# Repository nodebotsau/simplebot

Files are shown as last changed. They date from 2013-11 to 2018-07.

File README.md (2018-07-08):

# SimpleBot



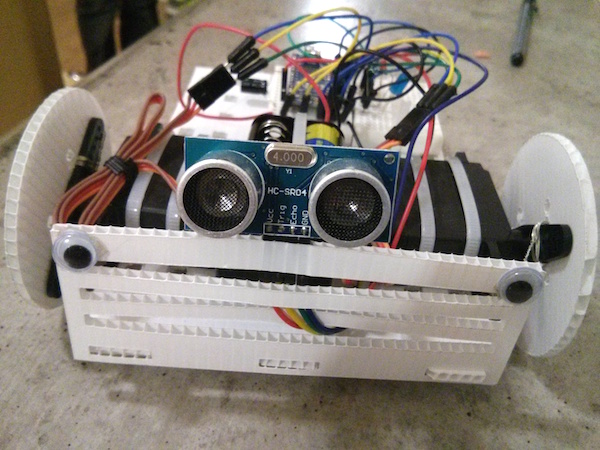
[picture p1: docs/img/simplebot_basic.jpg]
SimpleBot


## Overview

This is one of the most simple robots you can make. Features are:

* quick to put together (about an hour)
* very hackable (it can be built with cardboard, corflute or laser cut acrylic
or wood so very easily modifiable)
* can move pretty fast (at full tilt it will go about half a metre a second -
faster if you have more juice for the motors!)
* very extendable (much of the magic happens in code and sensors can be easily added)
* Cheap (costs less than AUD$100 which is very cheap for your first robot)

This bot is an adaptation of the excellent [SumoBot Jr](https://github.com/makenai/sumobot-jr/)
made by [Paweł Szymczykowski](http://twitter.com/makenai) but doesn't require
laser cutting wood or plastic to make. However you can laser cut it if you want
something a bit more long lasting.

## Capabilities

The SimpleBot can be tethered over USB or controlled via Bluetooth Serial or
over the network using WiFi. Your computer will do all the hard work of
control processing and interface control etc and just send messages to the
board to steer it.

If you get really sophisticated you can make it have some AI.

This is the very first prototype, put together in about 30 minutes one evening.

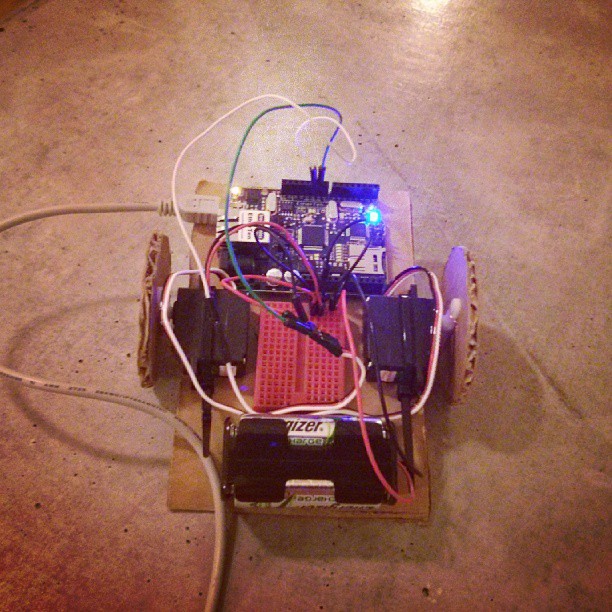
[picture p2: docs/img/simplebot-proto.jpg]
SimpleBot


As this is such a simple robot, once you've got it working you can then extend
it to make it much more capable including becoming wireless. This one has been
extended with a wifi module to untether it from your computer..

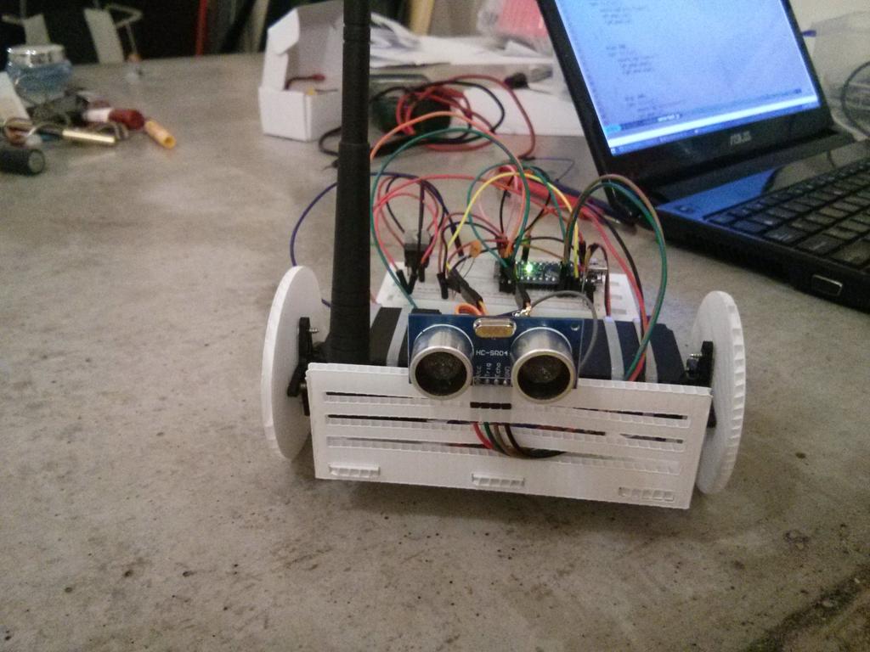
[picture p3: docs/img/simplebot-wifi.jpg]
SimpleBot MkII


Once you understand how things work you can reuse all of the components to
make a bigger, badder, faster robot and switch the cardboard for more durable
elements such as laser cut wood or plastic if you desire.
We've even [supplied the SVG and DXF files to do exactly that](/physical).

Add a raspberry pi and you get a SimplePiBot which can be made fully autonomous.

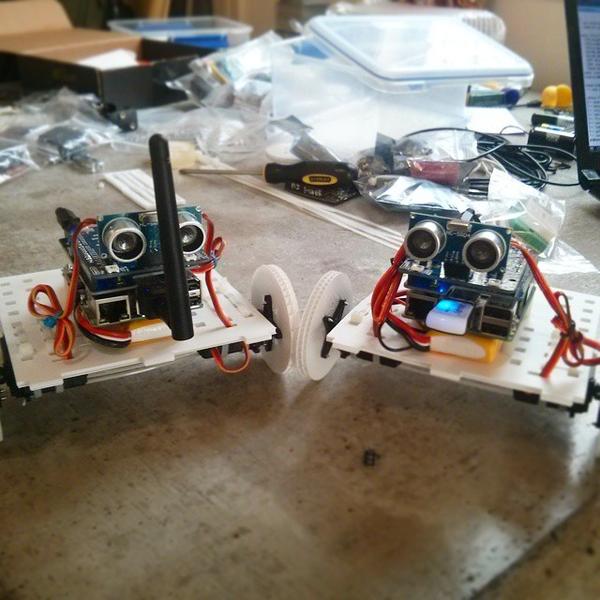
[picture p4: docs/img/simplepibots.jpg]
SimplePiBot


## Materials needed

The following are the various components you need to get hold of to make a basic
SimpleBot. If you're making this at a NodeBots event you'll have a set of
components in your kits.

|  # | Component | Notes |
|:--:|---|---|
|  1 | Arduino | We use Nanos because they are small and inexpensive (and light) but any arduino will do |
| 10 | M-M Jumper wires | The more the better but 10 will be enough to build with |
|  2 | DC Motors | These are common - get ones with wheels & gears |
|  1 | Battery pack | LiPo or 4xAA - about 5V is what you're after |
|  1 | Mini breadboard  | Smaller is better |
| 10 | Cable ties | 3-4mm wide and about 100-200mm long is a good size to work with. The more the better |

Other things you might want to add to your bot:

* Laser pointer to make an annoying cat toy.
* Stickers to bling out your bot.
* Spikes to take out others; Ben Hur or Mad Max style.
* USB WebCam if you want to give your bot some vision.
* USB cable extender if you want some range.
* Bluetooth or wireless modules to remove the USB cable.
* An Ultrasonic sensor to do obstacle detection
* Reflectance sensors to do line following

# Installation and setup

Start with the [installation process outlined here](https://github.com/nodebotsau/nbdau/blob/master/setup.md)
if you haven't already done so.

## Install the code dependencies

Clone the repo and install everything from here:

```
git clone https://github.com/nodebotsau/simplebot.git
cd simplebot
npm install
```

## Flashing the arduino

Use `interchange` to install the firmware to the arduino. Plug the arduino in
and then run the following command from your terminal.

```
interchange install hc-sr04 -a nano --firmata
```

Assuming you get no errors, you're good to go on that front.

## Run a basic blink program

Next, to test you've got Firmata running, run a basic blink program with the following command: 

```
node examples/blink.js
```

If it all goes well. You'll see a blinking LED positioned next to the L on your arduino.

```
[ ] RX
[ ] TX
[*] POW 
[*] L     <--- this light will start flashing
```

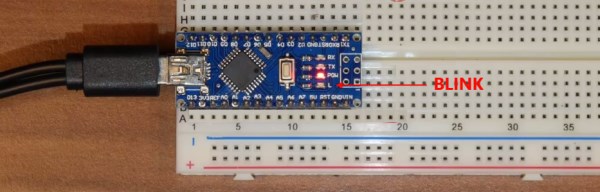
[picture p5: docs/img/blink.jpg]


Open the [`examples/blink.js`](examples/blink.js) program in an editor and look at the code. Its currently set to blink every 500ms. 

Try changing this to 100ms and see if it blinks faster now.

```js
board.on("ready", function() {
  var led = new five.Led(13);
  led.blink(500);  //  <--- try changing this value see if it blinks faster/slower
});
```

## Build a SimpleBot

You can go in a few different directions with the SimpleBot. Details for the
different styles can be found below however the common principles are
discussed in the next section.

* [SumoBot](docs/sumobot.md)
* [Line Follower](docs/linefollower.md)
* [Obstacle avoider](docs/obstacleavoider.md)

### Differential drive

Each SimpleBot is a little different because it's yours but the general principles
are the same. You have two motors, each of which drive a wheel - this is called
[differential drive](https://en.wikipedia.org/wiki/Differential_wheeled_robot) -
and the combination of these working together will drive the robot forward, backwards
and turn on the spot each way.

Use cable-ties (zip ties) to join everything to the chassis.

If you want to see a video explaining this in more detail there's a version
on [you tube](https://www.youtube.com/watch?v=KoACCjtkHIg) (this uses servos on
an older Mark III SimpleBot but the principle holds).

### Basic wiring

The wiring diagrams are provided here:

Schematic:

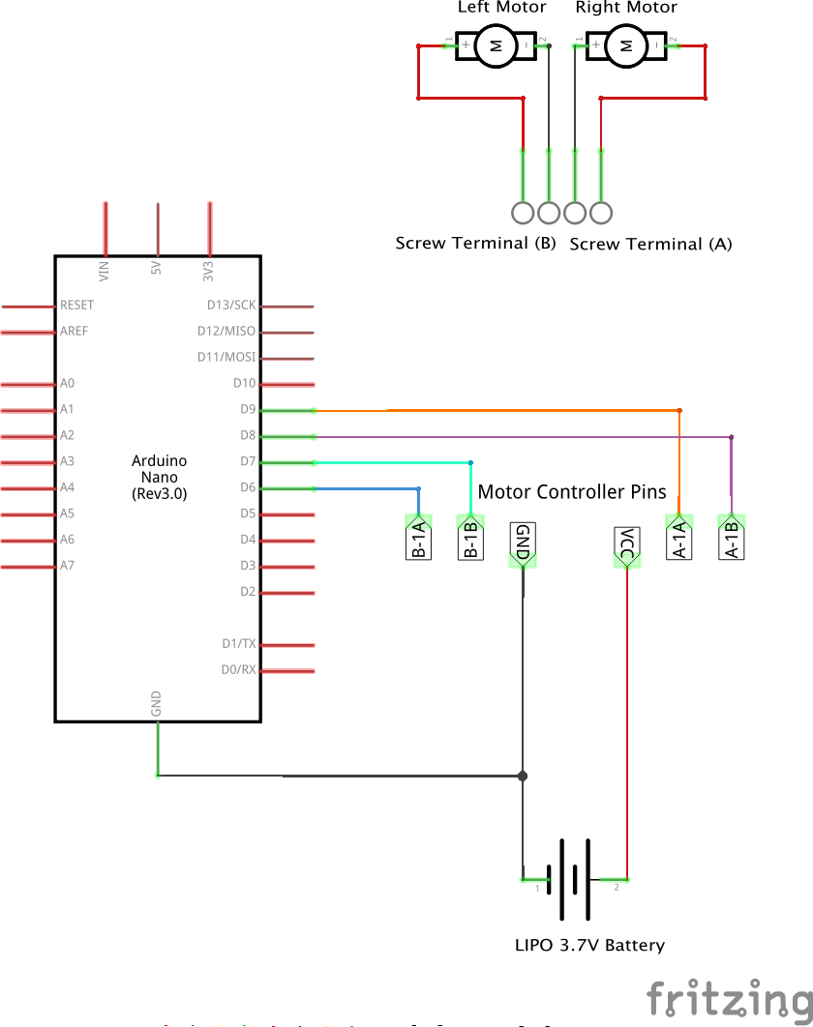
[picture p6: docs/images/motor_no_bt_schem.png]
SimpleBot schematic


# Examples

## A simple drive example

In the `examples` folder you can see an example called `motors.js` or
`servos.js` - choose the version depending on your motor types. This is
a very simple control example which uses the arrow and space keys on the keyboard
to drive the SimpleBot around.

Simply run:

```shell
node examples/motors.js SERIAL_DEVICE
```

```shell
node examples/servos.js SERIAL_DEVICE
```

Where `SERIAL_DEVICE` is the path to the serial port (eg `/dev/tty/USB0`).

You should now be able to drive your robot around happily. Go get a few friends
to build one too and you can have SumoBot Battles.

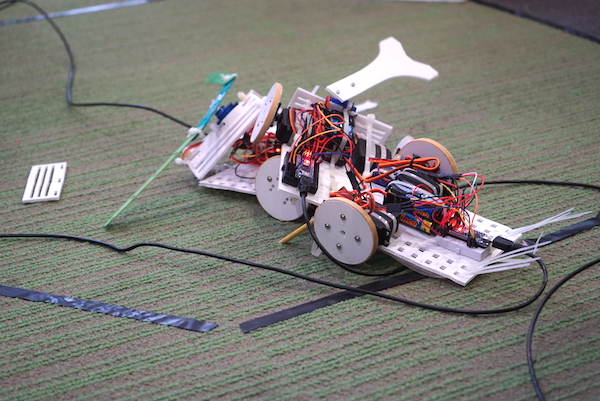
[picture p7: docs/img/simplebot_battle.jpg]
A simplebot battle royale at NodeBots Day


### Tuning servos

If you are using servos and they don't entirely stop then tune the stop value in the code by
setting a LSTOP and RSTOP value that is a little either side of 90 (this is
because CR servos are a hack and may need some tuning).

## Driving over Bluetooth

You can use bluetooth to drive the simplebot.

Get a bluetooth module and configure it. This is a mandatory step before you can
do it properly..

Per [this wiki entry in J5](https://github.com/rwaldron/johnny-five/wiki/Getting-Started-with-Johnny-Five-and-JY-MCU-Bluetooth-Serial-Port-Module)

### Wiring for BT.

Connect the BT Module TX pin to the Arduino RX pin and the BT Module RX pin to
the Arduino TX pin and you should be ready to go. Note that if you need to
flash the arduino or anything you need to unplug the BT module.

### Connecting

Once you've got your bluetooth set up, pair it with your computer so it appears
as a serial device.

Simply go:

```
node examples/motors.js /dev/tty.SERIALPORT
```

Changing the device path to whatever yours is to the Bluetooth Module. You
should now be able to drive using wireless over bluetooth just the same as
using a USB cable.

## Game controller

If you happen to have a playstation controller then you can use the
sb-controller.js example to drive your simplebot using a console controller
which is pretty cool.

# LICENSE NOTES

This SimpleBot repo is licensed using the MIT license for all components.

Firmata implementations are modifications of
[https://github.com/firmata/arduino/](Firmata for Arduino) by
[https://github.com/soundanalogous](Jeff Hoefs @soundanalagous) and others and
is used according to the GPL.

Firmata modifications include merged components of
the [https://github.com/jgautier/arduino-1/tree/pulseIn](pulseIn code) as
created by [https://github.com/jgautier](Julian Gautier @jgautier).

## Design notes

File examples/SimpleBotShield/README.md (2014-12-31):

# Using the SimpleBot Shield

If you have a SimpleBot shield you will need an arduino to go with it.

Key features of the shield are:

* Servo headers broken out for Left and Right wheels on pins 9 & 10
* Additional headers broken out for pins 2,3,5,6 using servo pin out style (sig, 5v, gnd)
* 4xWS2812b RGB LEDs (NeoPixels) on the corners of the board attached to pin 6
* Ultrasonic sensor broken out attached to pin 8
* Breakouts for Analog pins 1-5 using screw terminals
* I2C breakout for optional IMU9 module 

## Populating the board

Here are the [build instructions for the board](http://www.openhardwareconf.org/wiki/SimpleBot_Shield_Assembly).

More [detailed instructions](http://www.openhardwareconf.org/wiki/Surface_Mount_Assembly_for_SimpleBot_Shield) on soldering the WS2812 LEDs is available here.

## Preparing custom firmata

To use this shield in total you will need a custom version of firmata that
comprises all the additional libraries you need to make it work. This ships
as part of this repo in the firmware directory. You will need to use ino tool to
compile and upload this to the board so [follow the getting started directions](http://inotool.org/#installation) for
ino tool before attempting the next component.

To install firmata (and install all node dependencies also) follow the directions below.

```
cd ~
git clone https://github.com/nodebotsau/simplebot
cd simplebot
npm install
cd firmware/ino/SBSFirmata
ino clean && ino build -m uno
```

You should see the output of the build sequence and get a positive response from ino 
as below:

```
Searching for Board description file (boards.txt) ... /home/pi/arduino-1.0.5/hardware/arduino/boards.txt
Searching for Arduino lib version file (version.txt) ... /home/pi/arduino-1.0.5/lib/version.txt
Detecting Arduino software version ...  1.0.5 (1.0.5)
Searching for Arduino core library ... /home/pi/arduino-1.0.5/hardware/arduino/cores/arduino
Searching for Arduino variants directory ... /home/pi/arduino-1.0.5/hardware/arduino/variants
Searching for Arduino standard libraries ... /home/pi/arduino-1.0.5/libraries
Searching for make ... /usr/bin/make
Searching for avr-gcc ... /usr/bin/avr-gcc
Searching for avr-g++ ... /usr/bin/avr-g++
Searching for avr-ar ... /usr/bin/avr-ar
Searching for avr-objcopy ... /usr/bin/avr-objcopy
src/SBSFirmata.ino
Searching for Arduino lib version file (version.txt) ... /home/pi/arduino-1.0.5/lib/version.txt
Detecting Arduino software version ...  1.0.5 (1.0.5)
Scanning dependencies of src
Scanning dependencies of Servo
Scanning dependencies of neopixel
Scanning dependencies of ws2812
Scanning dependencies of Wire
Scanning dependencies of arduino
src/Firmata.cpp
src/SBSFirmata.cpp
Servo/Servo.cpp
Linking libServo.a
ws2812/ws2812.cpp
Linking libws2812.a
Wire/utility/twi.c
Wire/Wire.cpp
Linking libWire.a
neopixel/Adafruit_NeoPixel.cpp
Linking libneopixel.a
arduino/wiring_pulse.c
arduino/wiring_analog.c
arduino/WInterrupts.c
arduino/wiring_shift.c
arduino/avr-libc/malloc.c
arduino/avr-libc/realloc.c
arduino/wiring_digital.c
arduino/wiring.c
arduino/WString.cpp
arduino/new.cpp
arduino/Print.cpp
arduino/main.cpp
arduino/Stream.cpp
arduino/CDC.cpp
arduino/HID.cpp
arduino/USBCore.cpp
arduino/WMath.cpp
arduino/Tone.cpp
arduino/HardwareSerial.cpp
arduino/IPAddress.cpp
Linking libarduino.a
Linking firmware.elf
Converting to firmware.hex
```

Assuming no errors go ahead and upload using one of the options below.

If just a standard Arduino then:

    ino upload -m uno

If you're using a PiLeven then:

    ino upload -m uno -p /dev/ttyS99

You will get something similar to the following output:

```
Searching for stty ... /bin/stty
Searching for avrdude ... /home/pi/arduino-1.0.5/hardware/tools/avrdude
Searching for avrdude.conf ... /home/pi/arduino-1.0.5/hardware/tools/avrdude.conf
Guessing serial port ... /dev/ttyACM0

avrdude: AVR device initialized and ready to accept instructions

Reading | ################################################## | 100% 0.00s

avrdude: Device signature = 0x1e950f
avrdude: reading input file ".build/uno-620a679d/firmware.hex"
avrdude: writing flash (17628 bytes):

Writing | ################################################## | 100% 3.16s

avrdude: 17628 bytes of flash written
avrdude: verifying flash memory against .build/uno-620a679d/firmware.hex:
avrdude: load data flash data from input file .build/uno-620a679d/firmware.hex:
avrdude: input file .build/uno-620a679d/firmware.hex contains 17628 bytes
avrdude: reading on-chip flash data:

Reading | ################################################## | 100% 2.47s

avrdude: verifying ...
avrdude: 17628 bytes of flash verified

avrdude: safemode: Fuses OK

avrdude done.  Thank you.
```

If there's no errors then you now have the relevant firmata on your arduino for the
SimpleBot Shield.

## Using the examples

AS part of the repos, three examples are provided that are designed to work 
specifically to the shield. These are located in the same folder as this
README and are described below

All examples should be called from the root of the repo after having executed:

```
npm install
```

In order to install the node dependencies.

### simplebot.js 

This is a simple driving example taking input from the keyboard to drive your
SimpleBot around. The arrow keys drive it forward, backwards and turn it
left and right. Space will stop it.

To run, use the command below, substituting /dev/ttyS99 for the port of your
arduino for your environment.

```
nodejs examples/SimpleBotShield/simplebot.js /dev/ttyS99
```

### ping.js

This example shows how the ping sensor works and reports back the range in
cm and inches to an obstacle. 

To run, use the command below, substituting /dev/ttyACM0 for the port of your
arduino for your environment.

```
nodejs examples/SimpleBotShield/ping.js /dev/ttyACM0
```

Output will look like this (use Ctrl+C to quit):

```
1420024159594 Connected /dev/ttyACM0 
1420024159599 Repl Initialized 
>> Object is 15.259 cm away
Object is 5.98 inches away
Object is 33.431 cm away
Object is 13.1 inches away
```

### np.js

This example shows how the neopixels can be lit and will move a single pixel
clockwise around the board moving through different colours.

To run, use the command below, substituting /dev/ttyACM0 for the port of your
arduino in your environment.

```
nodejs examples/SimpleBotShield/np.js /dev/ttyACM0
```

If you review the code you can see a single pixel is being updated and cycling
through various color names. Pixel can take a few options as illustrated below:

```
// strip.color() applies to the whole set of LEDs
// strip.show() is required once you have made your color manipulations in order
// to latch the LED strip and make them work.

strip.color("#ff0000"); // set whole strip red

// You can use HTML CSS color names and RGB values will be created
strip.color("teal"); // sets strip to a blue-green color.

// You can also use RGB values if you desire as shown below
strip.color("rgb(0, 255, 0)"); // sets strip to green.

// individual pixels can be addressed as well.
var p = strip.pixel(1); // get second LED

// and colors work just the same way on individual pixels too.
p.color("#0000FF"); // set second pixel blue.

// calling color() by itself will return an object with the current color
p.color(); // returns {r:0, g:0, b:255, hexcode:"#0000ff", color:"blue"}
```

## Going further

There are plenty of things you can do with a simplebot shield for example:

* Use the pixels to give you blinkers when you turn
* Back up when you get too close to an obstacle.
* direct the LEDs and use it to signal another SimpleBot
* Make a bot that dances and lights up when you get a tweet.

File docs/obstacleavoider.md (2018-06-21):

# Physical layout and design considerations for an obstacle avoiding robot

This document explains some of the design considerations you might want to
think about when building your robot.

## Electronics

The core electronics are as discussed for the basic SimpleBot build. You should
have a robot you can control with a keyboard to drive around.

### Additional components

* 1x Ultrasonic range finder

The diagram below shows the electronics schematic for a basic set up.

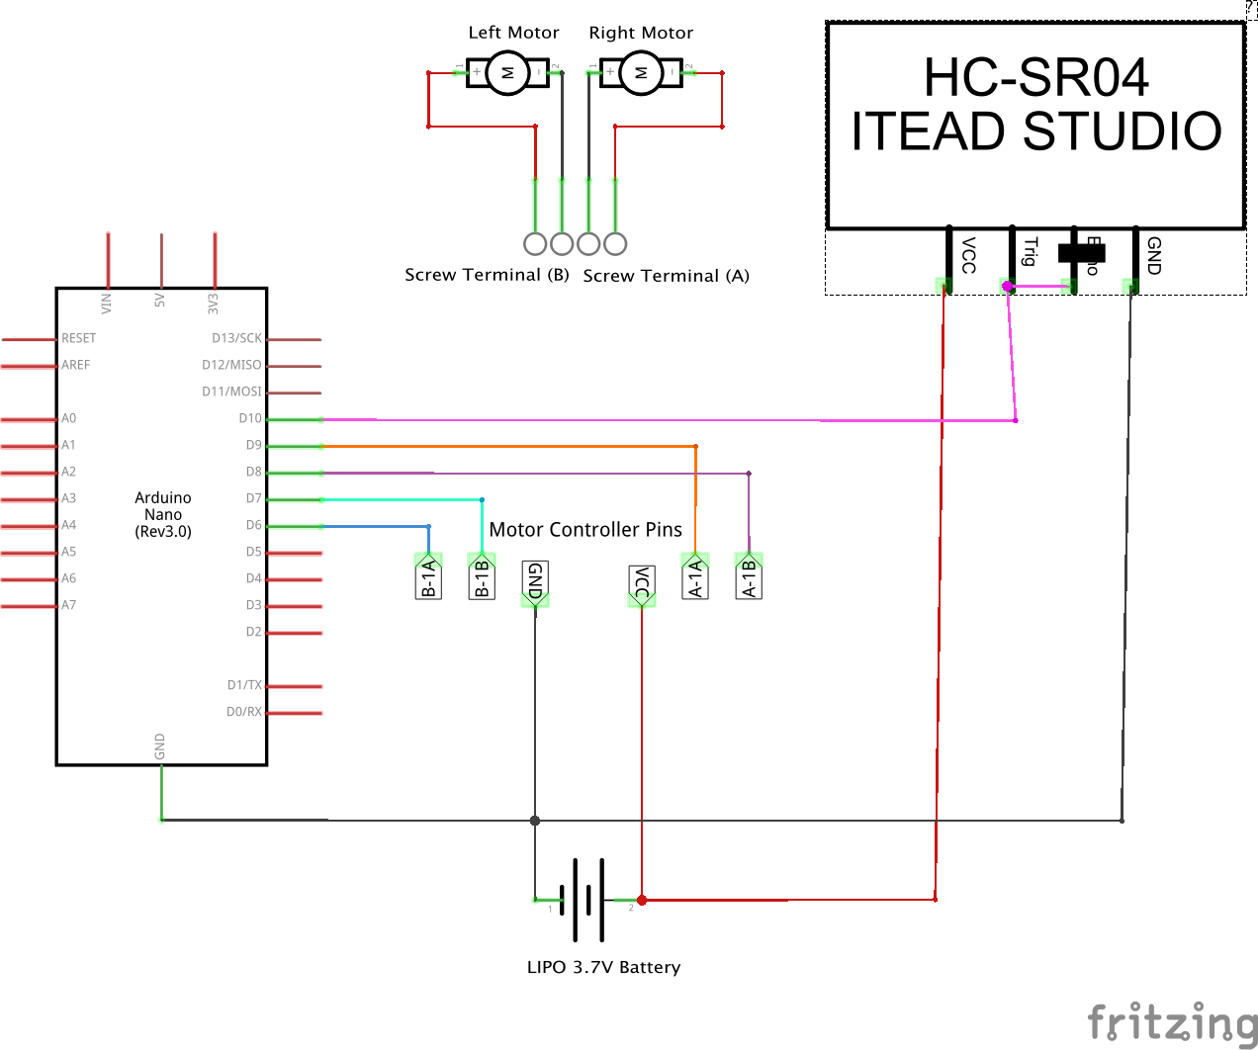
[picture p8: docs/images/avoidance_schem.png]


Note that the echo and trigger pins on the sensor are wired to the same pin
as the arduino can use both.

## Physical modifications

As you see the range finder looks like a pair of eyes and it does "see" like
a bat. As such you want to mount these on the front of your robot so they are
unobstructed. Cable ties work very well for this.

## Examples

In the `examples/simplebot-avoidance.js` file you can see a basic example that
will allow you to drive around until you get within 10cm of an obstacle and
then the SimpleBot will stop.

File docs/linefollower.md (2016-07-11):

# Physical layout and design considerations for a Line Following robot

This document explains some of the design considerations you might want to
think about when building your robot.

## Electronics

The core electronics are as discussed for the basic SimpleBot build. You should
have a robot you can control with a keyboard to drive around.

### Additional components

* 2x Reflectance sensors

The diagram below shows the electronics schematic for a basic set up.

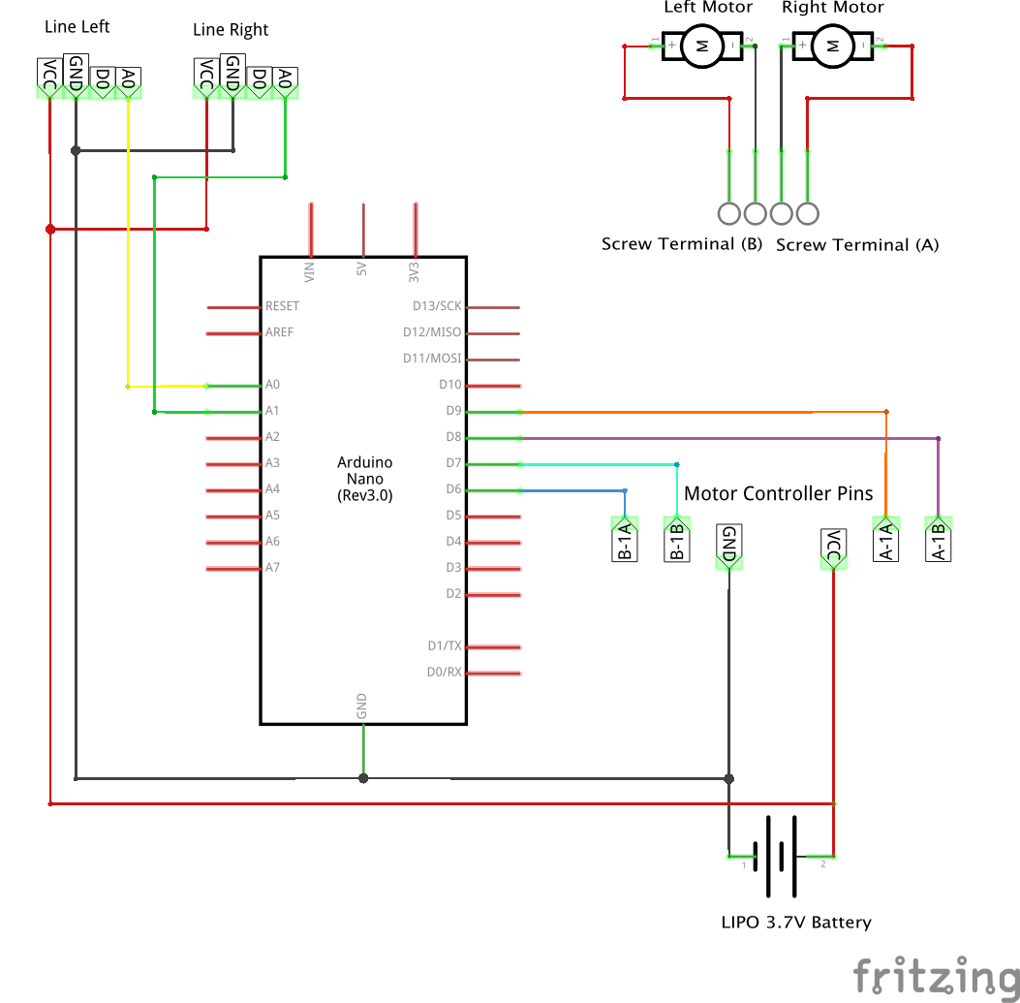
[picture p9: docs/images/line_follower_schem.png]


## Physical modifications

The reflectance sensors need to be pretty close to the ground, less than 1cm
is ideal. Mount them the same distance apart as the tape you'll be detecting.
What you want is for both sensors to be on the tape at the same time and you
can then tell when you are drifting off.

## Calibrating your sensors

Once you have the sensors wired up run `examples/calibrate-line.js` and
then slowly turn your bot back and forth over the line in order to get a sense
of what the minimum and maximum numbers it's seeing.

If you have a really contrasty surface you should get numbers close to 1023 for
full reflection and close to 0 for full absorption. The reality is you'll see
something inside that range.

Note down numbers that give you fairly definitive "on the line" and "off the line"
values.

## How line following works

The most simple line following algorithm is this:

```
// precondition: Both sensors start on the line

loop:
    drive both motors forward
    if (left sensor is off line):
        turn off right motor
    if (right sensor is off line):
        turn off left motor
```

This very simple code will check each of the sensors every time it loops. If
the sensor is on the line then that wheel will stay on as you want it to drive
forwards. If it comes off the line however, you turn the *opposite* wheel off
so that the wheel on the same side of the robot as the sensor is keeps driving.
This will pivot the bot back towards the line and it should move forwards again.

This algorithm is a naive approach and it does work but it is prone to
overshooting and not handling sharp turns. You can make it better with more
line sensors but also by reading the drift to see how much you've drifted or
for how long, this allows you to determine how much to turn back.

## Examples

In the `examples/simplebot-line.js` file you can see a basic example of this
algorithm in practice. If you put your bot on the test track and and run this
code you should see it slowly drive around the track, correcting its position
if it starts to drive off.

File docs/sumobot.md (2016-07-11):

# Physical layout and design considerations for a SumoBot

This document explains some of the design considerations you might want to
think about when building your robot.

## Electronics

The diagram below shows the electronics schematic for a basic set up.

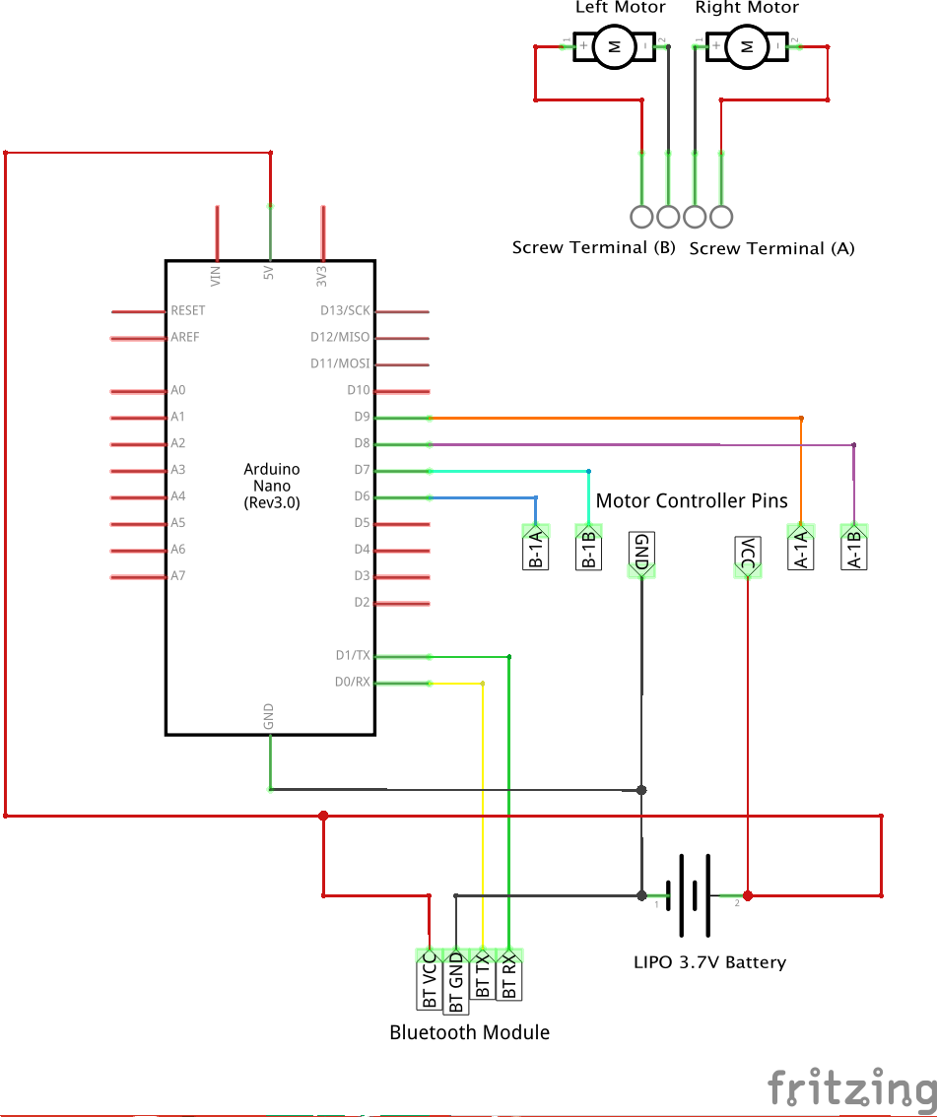
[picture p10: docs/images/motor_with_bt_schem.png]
Full schematic


If you do this however, once you move to bluetooth you may run into power
issues where the arduino resets on you. This will be particularly noticeable
when the battery is running flat. So what can you do?

First, keep your battery charged up. You have a charger to do exactly that so
use it. A full LiPo battery gives a nice solid voltage everything can use so
charge between tests and battles.

The second option is to use two batteries. One for your controllers and one for
your motors. The schematic for this is mostly the same except the VCC and GND
lines for your motors and servo connect to the second battery instead.

## Design styles

The maximum size of your bot is 25cm x 25cm x25cm - it has to fit inside that
to go in the ring. Too big and you're disqualified.

There are several design archetypes:

### The Wedge

This is a triangular wedge shape with the main aim being to stay low, move
fast and get under your opponent and run them out of the ring.

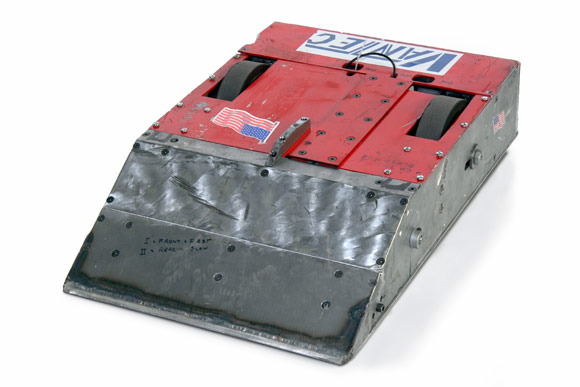
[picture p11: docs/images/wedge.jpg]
A perfect example of the Wedge


To do this effectively:

* Go as light as possible - everything extraneous must be removed
* Attempt to deliver as much speed as possible. This will affect your steering so
drivers need to practice rapid changes of direction and control.
* Traction is critical - when hit an opponent you need traction, make sure
your wheels will grip the floor.
* You need a wedge - it sounds obvious but your whole robot needs to be a wedge
to effectively slide under your opponent. Fabrication of this is critical.

Tactics:

The wedge is all about speed and out manoeuvring your oppenent, especially
those who are slow or have poor turning capability. Look for areas on the
opponent that are raised that will allow you to get underneath. Attack from a
weak side and go fast - don't be afraid to peel off and come back for another run.

### The Sumo

This design calls for weight. You'll move more slowly but with more mass. The
aim is to use your superior weight advantage to push the other opponent out
of the ring.

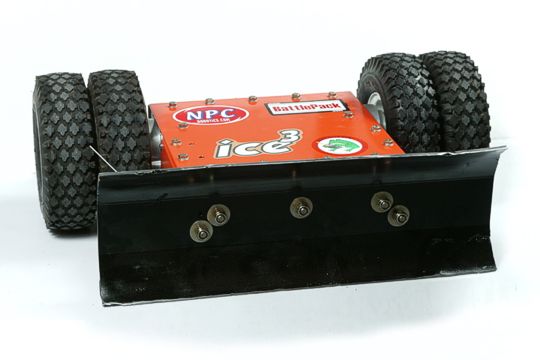
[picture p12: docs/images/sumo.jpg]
A tractor style design. Push, push, push!


To do this effectively:

* Look how you can weight your whole robot. Avoid just weighting one part as
this will make you unbalanced.
* You need traction. You're going to go slow, so deliver all the force you can
to your wheels.
* Protect your flanks - your turning speed will be poor so look at ways to
protect your sides (or better yet, make your bot usable in any direction not just
forwards).
* Snarl your opponent - if your opponent can't move then you can just grind them
out of the ring.

Tactics:

Slow and steady wins the bout. Stay to the middle until your opponent is nearby
then wait for them to try and attack you. Make sure you meet them head on and
then use your superior weight to just push them out of the circle. Don't get
caught on the edge.

### The flipper

Hard to pull off effectively, this design is all about winning in style. The aim is to
make a section of your bot that can use servos to flip an opponent. Once they
are incapable of moving, it's a simple task to push them out.

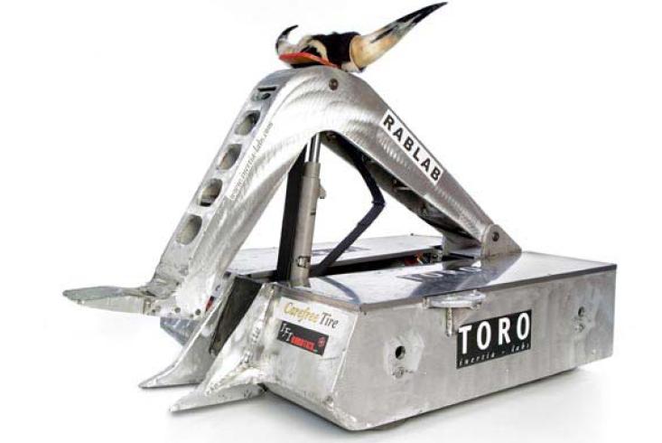
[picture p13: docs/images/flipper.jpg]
You definitely don't want to be anywhere near the front of this


To do this effectively:

* Keep your servo movement small. Servos move at a fixed speed and you want
this to happen fast to catch your opponent off guard. Use mechanical means to
amplify your servo movement into bigger actions.
* Practice your flips against things. It sounds obvious but does your flipper
flip?

Tactics:

Your objective is to close front on and then get your flipper under your
opponent. From there, ACTIVATE and turn that other bot over. Once you've
incapacitated your opponent, just push them out. Your flipper is your key
weapon so make sure you're bringing it to bear on your opponent.

### The whirlygig

This is possibly the craziest design, but pulled off well and it's brutally
effective. You aim is the wholesale destruction of your opponents' electronics
by using a whirling arm mounted on your bot.

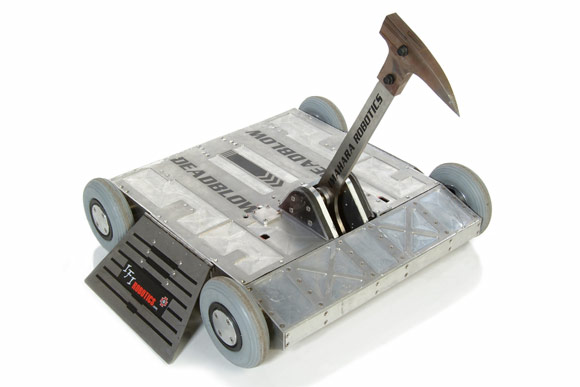
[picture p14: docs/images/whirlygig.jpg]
The pickaxe is a classic of this style


To do this effectively:

* Use servos attached to choppers or other mechanical means of wrecking your
opponent's systems.
* It makes you unbalanced but the higher you can come over the top of your
opponent the more chance you have to rip something important out of their
robot.
* Some particularly devastating whirlygigs just spear their opponent then drop
them outside the ring.

Tactics:

You really only have one objective, close with your opponent and unleash your
chopper, smasher, grabber or whirler as fast and as frequently as possible in
an attempt to maximise damage. A few stray wires ripped out and your opponent
will be dead in the ring. Use that opportunity to just ram them out of it.

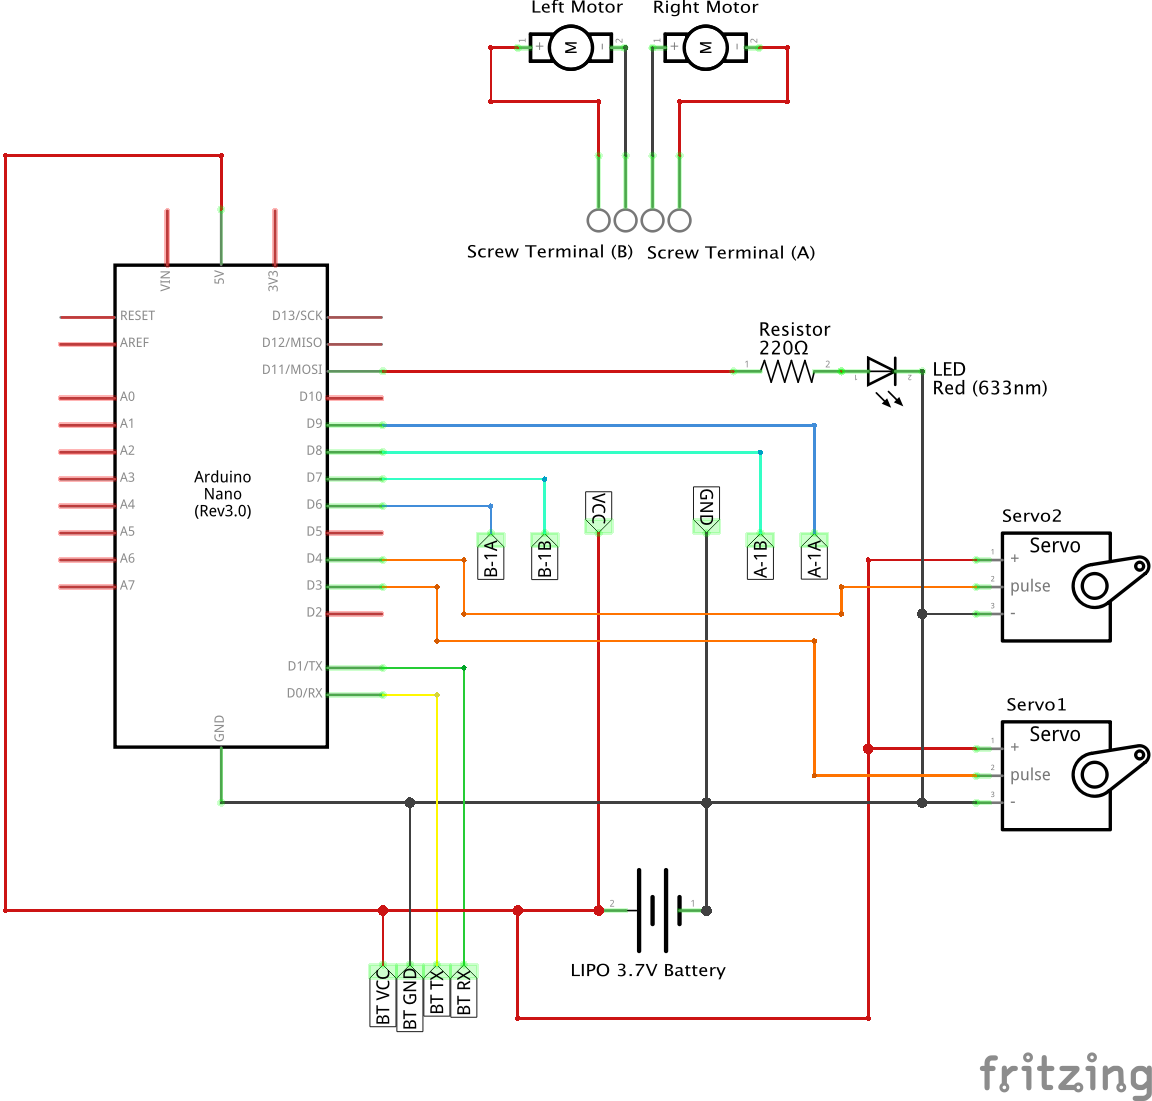
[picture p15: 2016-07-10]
docs/images/full_bot_schem.png

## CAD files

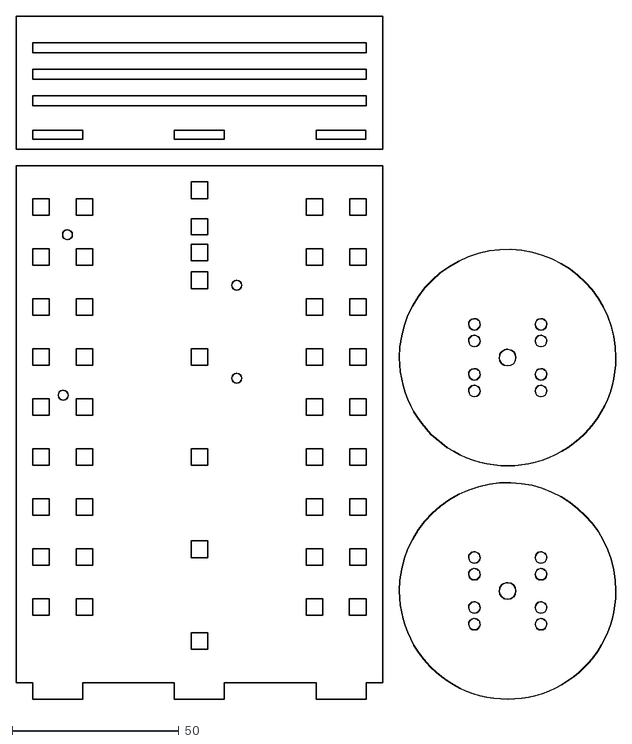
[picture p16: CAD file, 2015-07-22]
physical/plates.dxf
180.0 x 206.4

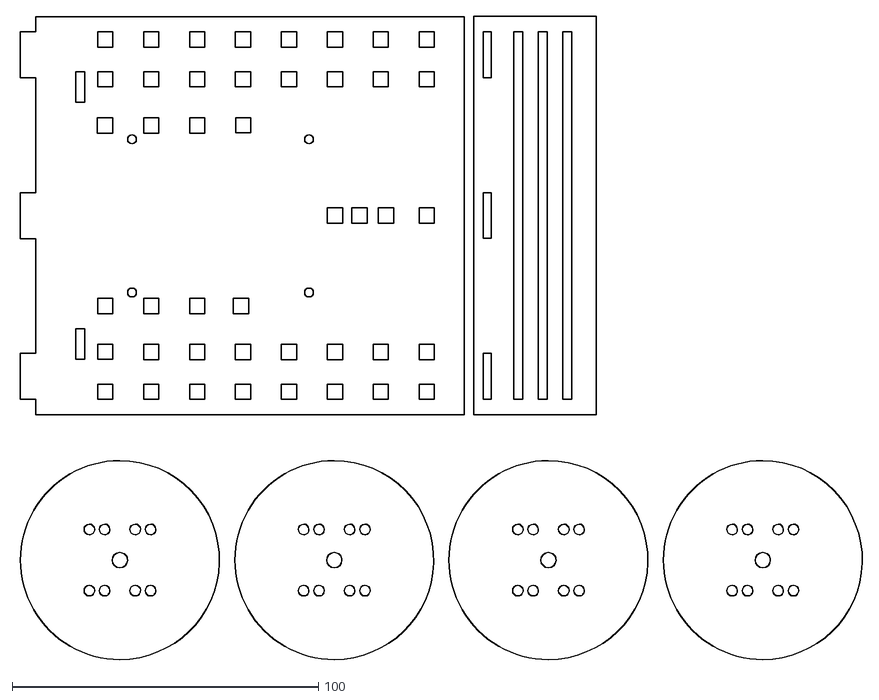
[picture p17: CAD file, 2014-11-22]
physical/plates-sbpi.dxf
276.6 x 210.0

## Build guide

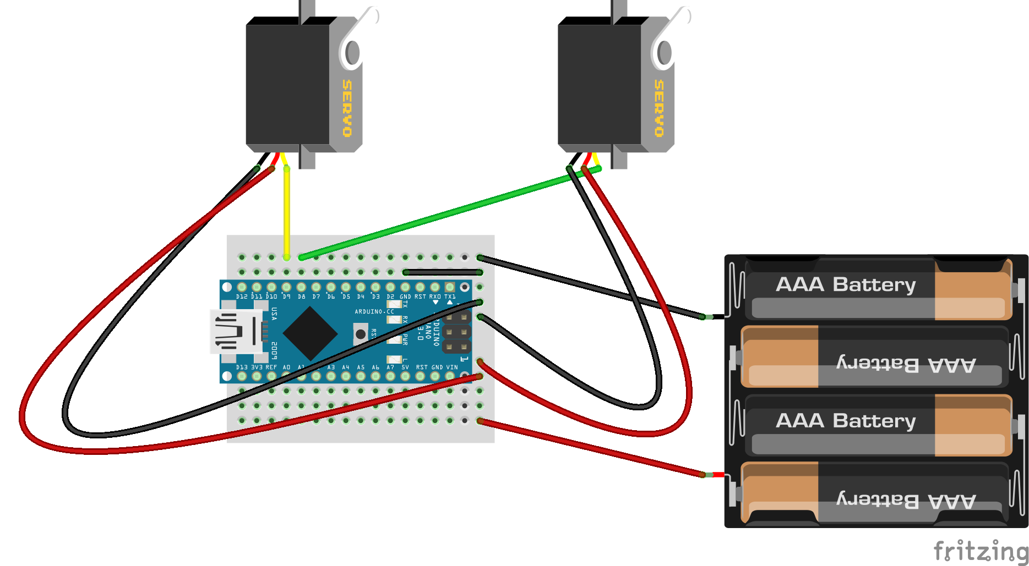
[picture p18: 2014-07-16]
examples/wiring/basic_wiring_bb.png

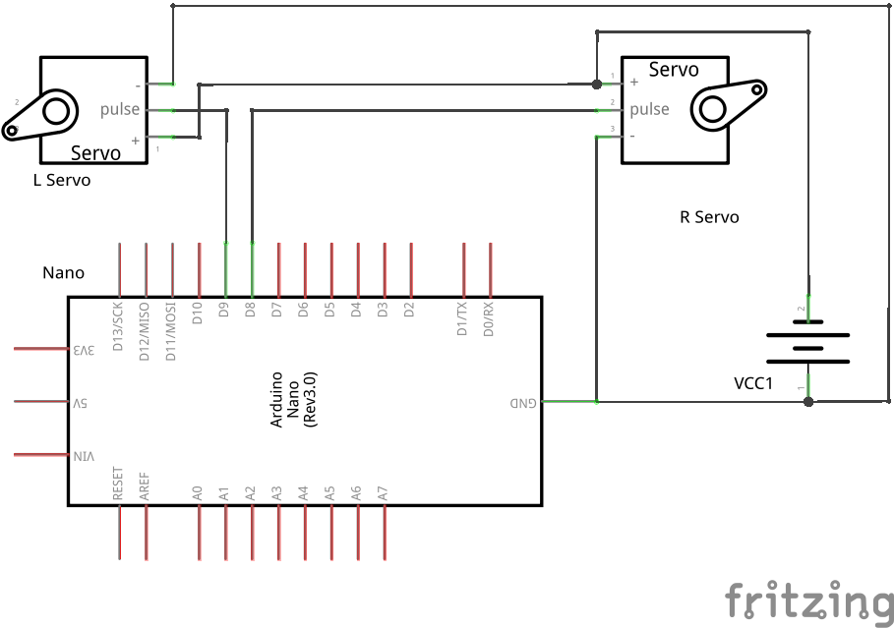
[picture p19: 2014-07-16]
examples/wiring/basic_wiring_schematic.png

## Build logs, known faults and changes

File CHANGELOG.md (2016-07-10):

# SimpleBot project changelog

## 0.6

* Updated dependecies for all packages
* Updated firmata to 2.5.1
* Simplified build process touse same core firmata and update relevant parts
for those targets that need it.
* Deploy bins for uno and nano for the firmware
* Added documentation for the different styles
* Updated readme docs generally.

## 0.5

* Removed some old cruft floating around
* Fixed dependencies to now build from node-pixel source rather than a lock copy
* Updated avoidance example to use Proximity class
* Fixed documentation to be up to date, link to build video and point to the
current serial bridge implementation for WiFi.
* Fixed `simplebot.js` code to be in line with the circuit diagram
* Broke out controller to be more reusable and updated examples with it.

## 0.4

* Updated all packages to latest versions
* changed build packages to use new grunt build process to make them
* Updated firmata to use new proximity firmata in line with J5
* updated examples to use new `Proximity class`
* Updated pixel for SBS to use new `node-pixel` version.
* Added firmware for ESP8266 transparent bridge
* Added example for network simplebot
* Added `network_simplebot_firmata`

## 0.3.2

* Removed some old cruft and old physical files no longer needed.
* Updated SimpleBot chassis with some mods to make simpler and no 3d printed part required.

## 0.3.1

* Added changelog, typos, fixed old NPM url.

## 0.3.0

* New variation added for Simple Pi Bot - RPi based SimpleBot, including new designed chassis.
* Significant repo restructure to accomodate SimpleBot Shield and ino build chain
* Brought in attribution and licenses for everything being used properly
* Migrated build tools to use ino for firmware rather than Arduino
* Updated firmata to latest stable version, 2.4 and ported @jgautier's pulseIn
modifications to it as well as wrapped previous work from RGBLED to use NeoPixels
* Merged example from @holodigm for collision avoidance (https://github.com/nodebotsau/simplebot/pull/12)
* Cleaned out any leostick cruft
* Updated libraries to latest stables.

### Contributor acknowledgments:

* [Alec Clews](https://github.com/alecthegeek) - Rasbian install scripts for RPi (https://github.com/alecthegeek/CCHS_Raspian_for_IoT)
* [Andy Gelme](https://github.com/geekscape) - Continued testing, design advice,
* [Angus Gratton](https://github.com/projectgus) - SimpleBot Shield design and bumper design mods
* [Kym McInerney](https://github.com/holodigm) - collision avoidance example
* [Rick Waldron](https://github.com/rwaldron) - Pixel API suggestions and deep firmata architecture discussion

## 0.2.0

Can't remember before this time.

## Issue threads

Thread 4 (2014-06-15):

Redo PCB using generic headers

ajfisher, 2014-06-15:
Need to rebuild the layout to use generic headers rather than the arduino board specific ones for the shield as this has things like ICSP breakouts etc which are not need. Also needs correct alignment of the holes for bolting to chassis properly.

Closed 2015-07-26.

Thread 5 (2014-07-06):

Grounds not connected

ajfisher, 2014-07-06:
Grounds not connected between the two ground pins in the uno power header and then that circuit and the one that connects to the servos.

ajfisher, 2015-08-11:
Resolved by virtue of new SBS from freetronics.

Closed 2015-08-11.

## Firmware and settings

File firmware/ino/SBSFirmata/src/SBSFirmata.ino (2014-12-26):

/*
 * Firmata is a generic protocol for communicating with microcontrollers
 * from software on a host computer. It is intended to work with
 * any host computer software package.
 *
 * To download a host software package, please clink on the following link
 * to open the download page in your default browser.
 *
 * http://firmata.org/wiki/Download
 */

/*
  Copyright (C) 2006-2008 Hans-Christoph Steiner.  All rights reserved.
  Copyright (C) 2010-2011 Paul Stoffregen.  All rights reserved.
  Copyright (C) 2009 Shigeru Kobayashi.  All rights reserved.
  Copyright (C) 2009-2014 Jeff Hoefs.  All rights reserved.

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
  See file LICENSE.txt for further informations on licensing terms.

  formatted using the GNU C formatting and indenting
*/

/*
 * TODO: use Program Control to load stored profiles from EEPROM
 */

/** MODIFIED BY AJFISHER to support the SimpleBotShield v1 **/

#include <Servo.h>
#include <Wire.h>
#include "./Firmata.h"

#include "neopixel/Adafruit_NeoPixel.h"
#include "ws2812/ws2812.h"

// move the following defines to Firmata.h?
#define I2C_WRITE B00000000
#define I2C_READ B00001000
#define I2C_READ_CONTINUOUSLY B00010000
#define I2C_STOP_READING B00011000
#define I2C_READ_WRITE_MODE_MASK B00011000
#define I2C_10BIT_ADDRESS_MODE_MASK B00100000

#define MAX_QUERIES 8
#define MINIMUM_SAMPLING_INTERVAL 10

#define REGISTER_NOT_SPECIFIED -1

#define PULSE_IN                0x74 // send a pulse in command

/*==============================================================================
 * GLOBAL VARIABLES
 *============================================================================*/

/* analog inputs */
int analogInputsToReport = 0; // bitwise array to store pin reporting

/* digital input ports */
byte reportPINs[TOTAL_PORTS];       // 1 = report this port, 0 = silence
byte previousPINs[TOTAL_PORTS];     // previous 8 bits sent

/* pins configuration */
byte pinConfig[TOTAL_PINS];         // configuration of every pin
byte portConfigInputs[TOTAL_PORTS]; // each bit: 1 = pin in INPUT, 0 = anything else
int pinState[TOTAL_PINS];           // any value that has been written

/* timer variables */
unsigned long currentMillis;        // store the current value from millis()
unsigned long previousMillis;       // for comparison with currentMillis
unsigned int samplingInterval = 19;          // how often to run the main loop (in ms)

/* i2c data */
struct i2c_device_info {
  byte addr;
  int reg;
  byte bytes;
};

/* for i2c read continuous more */
i2c_device_info query[MAX_QUERIES];

byte i2cRxData[32];
boolean isI2CEnabled = false;
signed char queryIndex = -1;
unsigned int i2cReadDelayTime = 0;  // default delay time between i2c read request and Wire.requestFrom()

Servo servos[MAX_SERVOS];
byte servoPinMap[TOTAL_PINS];
byte detachedServos[MAX_SERVOS];
byte detachedServoCount = 0;
byte servoCount = 0;


/*==============================================================================
 * CUSTOM CALLBACKS for NP processing
 *============================================================================*/

void pixelCallback(char *string) {

    String message = String(string);

    // now we have a message, let's parse it.
    int msg_index = message.lastIndexOf('{');
    if (msg_index >= 0) {
        parse_message(message, msg_index);
    }
    // Firmata bug: SysEx STRING_DATA handler uses malloc(), but not free()
    // https://github.com/firmata/arduino/issues/74

    //free(string);
    string = 0;
}

/*==============================================================================
 * FUNCTIONS
 *============================================================================*/

void attachServo(byte pin, int minPulse, int maxPulse)
{
  if (servoCount < MAX_SERVOS) {
    // reuse indexes of detached servos until all have been reallocated
    if (detachedServoCount > 0) {
      servoPinMap[pin] = detachedServos[detachedServoCount - 1];
      if (detachedServoCount > 0) detachedServoCount--;
    } else {
      servoPinMap[pin] = servoCount;
      servoCount++;
    }
    if (minPulse > 0 && maxPulse > 0) {
      servos[servoPinMap[pin]].attach(PIN_TO_DIGITAL(pin), minPulse, maxPulse);
    } else {
      servos[servoPinMap[pin]].attach(PIN_TO_DIGITAL(pin));
    }
  } else {
    Firmata.sendString("Max servos attached");
  }
}

void detachServo(byte pin)
{
  servos[servoPinMap[pin]].detach();
  // if we're detaching the last servo, decrement the count
  // otherwise store the index of the detached servo
  if (servoPinMap[pin] == servoCount && servoCount > 0) {
    servoCount--;
  } else if (servoCount > 0) {
    // keep track of detached servos because we want to reuse their indexes
    // before incrementing the count of attached servos
    detachedServoCount++;
    detachedServos[detachedServoCount - 1] = servoPinMap[pin];
  }

  servoPinMap[pin] = 255;
}

void readAndReportData(byte address, int theRegister, byte numBytes) {
  // allow I2C requests that don't require a register read
  // for example, some devices using an interrupt pin to signify new data available
  // do not always require the register read so upon interrupt you call Wire.requestFrom()
  if (theRegister != REGISTER_NOT_SPECIFIED) {
    Wire.beginTransmission(address);
#if ARDUINO >= 100
    Wire.write((byte)theRegister);
#else
    Wire.send((byte)theRegister);
#endif
    Wire.endTransmission();
    // do not set a value of 0
    if (i2cReadDelayTime > 0) {
      // delay is necessary for some devices such as WiiNunchuck
      delayMicroseconds(i2cReadDelayTime);
    }
  } else {
    theRegister = 0;  // fill the register with a dummy value
  }

  Wire.requestFrom(address, numBytes);  // all bytes are returned in requestFrom

  // check to be sure correct number of bytes were returned by slave
  if (numBytes < Wire.available()) {
    Firmata.sendString("I2C Read Error: Too many bytes received");
  } else if (numBytes > Wire.available()) {
    Firmata.sendString("I2C Read Error: Too few bytes received");
  }

  i2cRxData[0] = address;
  i2cRxData[1] = theRegister;

  for (int i = 0; i < numBytes && Wire.available(); i++) {
#if ARDUINO >= 100
    i2cRxData[2 + i] = Wire.read();
#else
    i2cRxData[2 + i] = Wire.receive();
#endif
  }

  // send slave address, register and received bytes
  Firmata.sendSysex(SYSEX_I2C_REPLY, numBytes + 2, i2cRxData);
}

void outputPort(byte portNumber, byte portValue, byte forceSend)
{
  // pins not configured as INPUT are cleared to zeros
  portValue = portValue & portConfigInputs[portNumber];
  // only send if the value is different than previously sent
  if (forceSend || previousPINs[portNumber] != portValue) {
    Firmata.sendDigitalPort(portNumber, portValue);
    previousPINs[portNumber] = portValue;
  }
}

/* -----------------------------------------------------------------------------
 * check all the active digital inputs for change of state, then add any events
 * to the Serial output queue using Serial.print() */
void checkDigitalInputs(void)
{
  /* Using non-looping code allows constants to be given to readPort().
   * The compiler will apply substantial optimizations if the inputs
   * to readPort() are compile-time constants. */
  if (TOTAL_PORTS > 0 && reportPINs[0]) outputPort(0, readPort(0, portConfigInputs[0]), false);
  if (TOTAL_PORTS > 1 && reportPINs[1]) outputPort(1, readPort(1, portConfigInputs[1]), false);
  if (TOTAL_PORTS > 2 && reportPINs[2]) outputPort(2, readPort(2, portConfigInputs[2]), false);
  if (TOTAL_PORTS > 3 && reportPINs[3]) outputPort(3, readPort(3, portConfigInputs[3]), false);
  if (TOTAL_PORTS > 4 && reportPINs[4]) outputPort(4, readPort(4, portConfigInputs[4]), false);
  if (TOTAL_PORTS > 5 && reportPINs[5]) outputPort(5, readPort(5, portConfigInputs[5]), false);
  if (TOTAL_PORTS > 6 && reportPINs[6]) outputPort(6, readPort(6, portConfigInputs[6]), false);
  if (TOTAL_PORTS > 7 && reportPINs[7]) outputPort(7, readPort(7, portConfigInputs[7]), false);
  if (TOTAL_PORTS > 8 && reportPINs[8]) outputPort(8, readPort(8, portConfigInputs[8]), false);
  if (TOTAL_PORTS > 9 && reportPINs[9]) outputPort(9, readPort(9, portConfigInputs[9]), false);
  if (TOTAL_PORTS > 10 && reportPINs[10]) outputPort(10, readPort(10, portConfigInputs[10]), false);
  if (TOTAL_PORTS > 11 && reportPINs[11]) outputPort(11, readPort(11, portConfigInputs[11]), false);
  if (TOTAL_PORTS > 12 && reportPINs[12]) outputPort(12, readPort(12, portConfigInputs[12]), false);
  if (TOTAL_PORTS > 13 && reportPINs[13]) outputPort(13, readPort(13, portConfigInputs[13]), false);
  if (TOTAL_PORTS > 14 && reportPINs[14]) outputPort(14, readPort(14, portConfigInputs[14]), false);
  if (TOTAL_PORTS > 15 && reportPINs[15]) outputPort(15, readPort(15, portConfigInputs[15]), false);
}

// -----------------------------------------------------------------------------
/* sets the pin mode to the correct state and sets the relevant bits in the
 * two bit-arrays that track Digital I/O and PWM status
 */
void setPinModeCallback(byte pin, int mode)
{
  if (pinConfig[pin] == I2C && isI2CEnabled && mode != I2C) {
    // disable i2c so pins can be used for other functions
    // the following if statements should reconfigure the pins properly
    disableI2CPins();
  }
  if (IS_PIN_DIGITAL(pin) && mode != SERVO) {
    if (servoPinMap[pin] < MAX_SERVOS && servos[servoPinMap[pin]].attached()) {
      detachServo(pin);
    }
  }
  if (IS_PIN_ANALOG(pin)) {
    reportAnalogCallback(PIN_TO_ANALOG(pin), mode == ANALOG ? 1 : 0); // turn on/off reporting
  }
  if (IS_PIN_DIGITAL(pin)) {
    if (mode == INPUT) {
      portConfigInputs[pin / 8] |= (1 << (pin & 7));
    } else {
      portConfigInputs[pin / 8] &= ~(1 << (pin & 7));
    }
  }
  pinState[pin] = 0;
  switch (mode) {
    case ANALOG:
      if (IS_PIN_ANALOG(pin)) {
        if (IS_PIN_DIGITAL(pin)) {
          pinMode(PIN_TO_DIGITAL(pin), INPUT); // disable output driver
          digitalWrite(PIN_TO_DIGITAL(pin), LOW); // disable internal pull-ups
        }
        pinConfig[pin] = ANALOG;
      }
      break;
    case INPUT:
      if (IS_PIN_DIGITAL(pin)) {
        pinMode(PIN_TO_DIGITAL(pin), INPUT); // disable output driver
        digitalWrite(PIN_TO_DIGITAL(pin), LOW); // disable internal pull-ups
        pinConfig[pin] = INPUT;
      }
      break;
    case OUTPUT:
      if (IS_PIN_DIGITAL(pin)) {
        digitalWrite(PIN_TO_DIGITAL(pin), LOW); // disable PWM
        pinMode(PIN_TO_DIGITAL(pin), OUTPUT);
        pinConfig[pin] = OUTPUT;
      }
      break;
    case PWM:
      if (IS_PIN_PWM(pin)) {
        pinMode(PIN_TO_PWM(pin), OUTPUT);
        analogWrite(PIN_TO_PWM(pin), 0);
        pinConfig[pin] = PWM;
      }
      break;
    case SERVO:
      if (IS_PIN_DIGITAL(pin)) {
        pinConfig[pin] = SERVO;
        if (servoPinMap[pin] == 255 || !servos[servoPinMap[pin]].attached()) {
          // pass -1 for min and max pulse values to use default values set
          // by Servo library
          attachServo(pin, -1, -1);
        }
      }
      break;
    case I2C:
      if (IS_PIN_I2C(pin)) {
        // mark the pin as i2c
        // the user must call I2C_CONFIG to enable I2C for a device
        pinConfig[pin] = I2C;
      }
      break;
    default:
      Firmata.sendString("Unknown pin mode"); // TODO: put error msgs in EEPROM
  }
  // TODO: save status to EEPROM here, if changed
}

void analogWriteCallback(byte pin, int value)
{
  if (pin < TOTAL_PINS) {
    switch (pinConfig[pin]) {
      case SERVO:
        if (IS_PIN_DIGITAL(pin))
          servos[servoPinMap[pin]].write(value);
        pinState[pin] = value;
        break;
      case PWM:
        if (IS_PIN_PWM(pin))
          analogWrite(PIN_TO_PWM(pin), value);
        pinState[pin] = value;
        break;
    }
  }
}

void digitalWriteCallback(byte port, int value)
{
  byte pin, lastPin, mask = 1, pinWriteMask = 0;

  if (port < TOTAL_PORTS) {
    // create a mask of the pins on this port that are writable.
    lastPin = port * 8 + 8;
    if (lastPin > TOTAL_PINS) lastPin = TOTAL_PINS;
    for (pin = port * 8; pin < lastPin; pin++) {
      // do not disturb non-digital pins (eg, Rx & Tx)
      if (IS_PIN_DIGITAL(pin)) {
        // only write to OUTPUT and INPUT (enables pullup)
        // do not touch pins in PWM, ANALOG, SERVO or other modes
        if (pinConfig[pin] == OUTPUT || pinConfig[pin] == INPUT) {
          pinWriteMask |= mask;
          pinState[pin] = ((byte)value & mask) ? 1 : 0;
        }
      }
      mask = mask << 1;
    }
    writePort(port, (byte)value, pinWriteMask);
  }
}


// -----------------------------------------------------------------------------
/* sets bits in a bit array (int) to toggle the reporting of the analogIns
 */
//void FirmataClass::setAnalogPinReporting(byte pin, byte state) {
//}
void reportAnalogCallback(byte analogPin, int value)
{
  if (analogPin < TOTAL_ANALOG_PINS) {
    if (value == 0) {
      analogInputsToReport = analogInputsToReport &~ (1 << analogPin);
    } else {
      analogInputsToReport = analogInputsToReport | (1 << analogPin);
      // Send pin value immediately. This is helpful when connected via
      // ethernet, wi-fi or bluetooth so pin states can be known upon
      // reconnecting.
      Firmata.sendAnalog(analogPin, analogRead(analogPin));
    }
  }
  // TODO: save status to EEPROM here, if changed
}

void reportDigitalCallback(byte port, int value)
{
  if (port < TOTAL_PORTS) {
    reportPINs[port] = (byte)value;
    // Send port value immediately. This is helpful when connected via
    // ethernet, wi-fi or bluetooth so pin states can be known upon
    // reconnecting.
    if (value) outputPort(port, readPort(port, portConfigInputs[port]), true);
  }
  // do not disable analog reporting on these 8 pins, to allow some
  // pins used for digital, others analog.  Instead, allow both types
  // of reporting to be enabled, but check if the pin is configured
  // as analog when sampling the analog inputs.  Likewise, while
  // scanning digital pins, portConfigInputs will mask off values from any
  // pins configured as analog
}

/*==============================================================================
 * SYSEX-BASED commands
 *============================================================================*/
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
void loop()
{
  byte pin, analogPin;

  /* DIGITALREAD - as fast as possible, check for changes and output them to the
   * FTDI buffer using Serial.print()  */
  checkDigitalInputs();

  /* SERIALREAD - processing incoming messagse as soon as possible, while still
   * checking digital inputs.  */
  while (Firmata.available())
    Firmata.processInput();

  /* SEND FTDI WRITE BUFFER - make sure that the FTDI buffer doesn't go over
   * 60 bytes. use a timer to sending an event character every 4 ms to
   * trigger the buffer to dump. */

  currentMillis = millis();
  if (currentMillis - previousMillis > samplingInterval) {
    previousMillis += samplingInterval;
    /* ANALOGREAD - do all analogReads() at the configured sampling interval */
    for (pin = 0; pin < TOTAL_PINS; pin++) {
      if (IS_PIN_ANALOG(pin) && pinConfig[pin] == ANALOG) {
        analogPin = PIN_TO_ANALOG(pin);
        if (analogInputsToReport & (1 << analogPin)) {
          Firmata.sendAnalog(analogPin, analogRead(analogPin));
        }
      }
    }
    // report i2c data for all device with read continuous mode enabled
    if (queryIndex > -1) {
      for (byte i = 0; i < queryIndex + 1; i++) {
        readAndReportData(query[i].addr, query[i].reg, query[i].bytes);
      }
    }
  }
}

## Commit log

2013-11-10 version 2.3 of the base and bumper plates - post Nov 9 workshop session
2013-11-10 additional lines of holes and bumper strips pre pathing
2013-11-11 DXF for cutting
    [plates.dxf]
2013-11-12 modded bumper to be taller & better fit holes
    [plates.dxf]
2013-11-12 added MeshThing holes for @geekscape and flipped one bumper
    [plates.dxf]
2013-11-16 Physical file clean up
    [plates.dxf]
2013-11-16 Added skid to the phsyical files from tinkercad
    [base_skid.stl]
2013-11-17 Add original wheel 1.0 DXF and improved wheel 1.1 CamBam files.
    [wheel.1.0.dxf]
2013-11-29 couple of small tweaks to the simplebot code and some attribution to @makenai
2014-05-24 Added pulsein support for ultrasonic sensor
2014-05-25 example using the piezo alongside the ultrasonic sensor
2014-06-15 first commit of a PCB 'shield' for Uno and Nano. Fritzing and Gerber files.
    [simplebotpcb.fzz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]
2014-07-07 major refactor of layout, servo, wifi, batt pos changes. All A() pins now connected
    [simplebotpcb.fzz]
2014-07-07 added gerbers
    [simplebotpcb_copperBottom.gbl, simplebotpcb_copperTop.gtl, simplebotpcb_maskBottom.gbs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]
2014-07-16 Latest iteration on SimpleBot base design. Added feet to make a soccer bot. Optimised for 3mm acryclic and coreflute
    [foot.dxf, plates.dxf, skid.stl]
2014-07-16 mods for setup document, included circuit diagrams and moved leostick bits around
    [basic_wiring.fzz]
2014-07-28 fixed an issue with grounds not connecting through digital pin side of arduino footprint to main link
    [simplebotpcb.fzz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]
2014-10-04 Added a printed - non laser cut version of bases
2014-10-06 removed rogue LED that had crept in
2014-11-22 SimpleBot Pi Version design files added
    [plates-sbpi.dxf]
2014-11-22 Latest CamBam files ready for corflute cut
2014-12-22 Updated ping to map to shield pin out
2014-12-31 Switched pixel lib to use es6-collections as shim for weakmap
2015-07-07 updated plates to have cable tie hook
    [plates.dxf]
2015-07-07 removed old files and updated docs
    [base_skid.stl, foot.dxf, simplebotpcb.fzz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]
2015-07-07 0.3.2 updates to new layout for chassis
2015-07-22 Mods to the DXF for the plates
    [plates.dxf]
2015-07-23 added the CH340 drivers for the nanos
2015-07-24 Added upd transparent serial for wireless simplebots
2015-09-09 Fix to make centred servo
2016-07-10 Mods to documentation
    [full_bot.fzz]
2016-07-11 Documentation updates
    [avoidance.fzz, line_follower.fzz, motor_no_bt.fzz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]
2016-07-21 Mods to bring driver up to date
2016-07-23 dependency updates and fix to motors.js for stdin processor
2016-07-23 Fix motors example
2017-06-08 Simplified motor example
2017-07-05 Clean up motor examples
    * Drop servos support
    * Drop all speed controls as it is a little flakey
    * Remove info about non-existent help
    * Document Q for quit (formerly C)
    * Make formatting consistent
2017-07-07 Removed drivers, simplified setup and pointed to master setup readme
2017-07-15 Make sure board can receive instructions (to avoid errors during warmup)
